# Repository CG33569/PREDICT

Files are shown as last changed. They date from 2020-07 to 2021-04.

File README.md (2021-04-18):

# PREDICT Project #

PREDICT Project at Aalborg University (AAU). This project is shared with Technical University of Denmark (DTU).
The project is focused on drone flight controller design and development, using a Real-Time Operative System implemented on a FPGA.

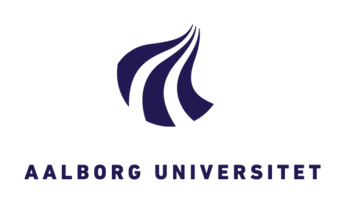
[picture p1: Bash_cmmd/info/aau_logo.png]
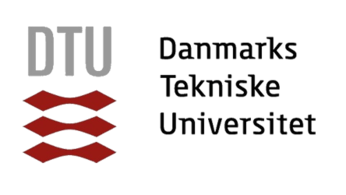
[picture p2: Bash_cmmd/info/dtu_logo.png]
 





### Repository structure ###

##### Documentation #####

An overview and general description of this project is included in Microsoft Power Point format, see the Predict Handover presentation.pptx file.

On top of that, the complete report is also included in PDF format, see the Predict_doc.pdf file. For more details, the original Latex files of the document are inside the Predict_doc folder. In case of needing to re-build the document, use doxigen or pdflatex commands, such as:

```
cd ~/REPO_LOCATION/PREDICT/Predict_doc && pdflatex main.tex
```

The documentation provides a detailed description about the project goals, functionalities and implementation. Additionally, it includes at the end two appendices as tutorial chapters to build a drone, calibrate it and run the flight controller on it.

##### Hardware - Drone desgin #####

Two models (A and B) were developed for this project. The related files are on the folder hardware_design, which contains:

* Printed Circuit Board (PCB folder): a custom board desgined for this project, which connects all the components to the controller. Designed with DipTrace

* Mechanics design (CAD_files folder): all the body and custom parts assembly for both models. Done in Solidworks 2019.

* Simulation model (simulation folder): both models A and B imported into CoppeliaSim simulator and additional dependencies for using the flight controller with the simulator.

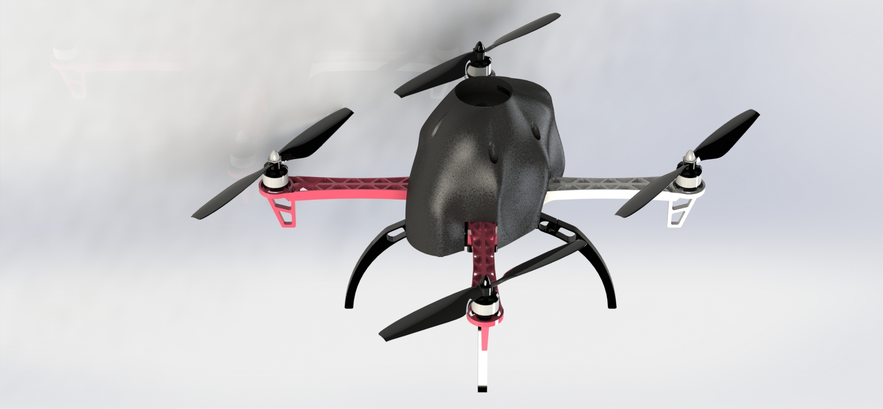
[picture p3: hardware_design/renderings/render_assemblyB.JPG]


##### Software - Flight controller and other applications #####

The flight controller is designed for the Patmos architechture, specifically for the de10-nano FPGA. A copy of this architecture is on the flight_controller/de10-nano-drone folder, which is a project on Quartus Prime.

The flight controller works as an application on that runs on top of the Patmos architecture. This C application is located on the flight/controller/de10-nano folder and it has the following:

* Basic functionalities (basic_lib folder): header and external files with global variables, low-level and functionalities related mostly to Patmos and communication.

* Components (sensors folder): header files for handling and using all the components.

* Flying functionalities (FC_functionalities folder): header files for calibration and flying modes available.

* Test programs (sensors_tests folder): header and script files for running the test programs.

* Main flight controller files (Flight_controller_v2.c and PREDICTthread.h).

##### Others #####

In case of being new to Patmos architecture, the folder Bash_cmmd contains scripts and configuration files that are useful to download, compile and build the T-Crest repositories and also for downloading C-apps in a de10-nano board. 
These scripts and files are explained in detail in the Predict documentation, on the Appendices (Chapters 7 and 8).

##### References #####

The main reference for this project is the Arduino Quadcopter project from [Brooking](http://www.brokking.net/ymfc-32_main.html) and part of his project is on the Arduino_project folder. 

Apart from that, all other references are listed on the Predict project documentation, the Bibliography section.

-----------------------------------------------

### Authors ####

* Carolina Gomez Salvatierra, cgomez19@student.aau.dk

* Rahul Ravichandran, rravic19@student.aau.dk

* Mark Adamik, madami15@student.aau.dk

Supervisor: Anders la Cour-Harbo, alc@es.aau.dk

-----------------------------------------------

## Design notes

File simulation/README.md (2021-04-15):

# PREDICT Drone in CoppeliaSim #

This a test-application for connecting the DE10-Nano FPGA to the CoppeliaSim simulator and try to use the flight controller on it. The idea is that the user can control the drone with the transmitter, the flight controller runs on the board but it gets the feedback and moves the drone in the simulation.

### Simulator CoppeliaSim set-up ###

Download the simulator (version EDU) from its [official website](https://www.coppeliarobotics.com/downloads).

Use the ExternalAPI to access from the FPGA-Simulator Interface the components inside the simulator.

Make sure you have following files in your directory, in order to run the various examples:

1. sim.py
2. simConst.py
3. the appropriate remote API library: "remoteApi.dll" (Windows), "remoteApi.dylib" (Mac) or "remoteApi.so" (Linux)
4. simpleTest.py (or any other example file) <- Run this script to verify that the connection between Coppelia and a Python scrip is successful.
5. Launch and start the simulation in drone_remoteAPI.ttt.

### FPGA and application set-up ###

1. Download on the FPGA the Quartus project "de10_nano_drone_simulator.jic" and re-start the board.
2. Connect the receiver and a UART-USB adapter on the uart3 of the board. See bellow the GPIO0 pins:

```
       * *
       * *
       * *
       * *
       * *
       * *
       * *
       * *
txd 26 * * 25 rxd UART3
AC3 24 * *
AC3 22 * *
AC3 20 * *
AC2 18 * *
AC1 16 * *
AC0 14 * *
       * *
       * *
       * *
       * *  
       * *  
txd  2 * *  1 rxd UART
```

Before doing the next steps, start the simulation in CoppeliaSim.

3. Download this C application as the simulation.c file as the main script.
4. At the same time, launch the main.py on the PC, which works as an interface between the simulator and the FPGA.

```
+--------------+         +--------------+         +-------------------+
|     FPGA     | <-----> |  Interface   | <-----> |     Simulator     |
| simulation.c |         |    main.py   |         |drone_remoteAPI.ttt|
+--------------+         +--------------+         +-------------------+
                        |___________________ PC ______________________|
```

##### Future works #####

* The current code only gets the receiver chanels 0-3 values on the simulation in order to spin the motors, but there is no controller avaliable yet.
* Improve the physics dynamics on the drone body so it can be controlled with a PID.
* Re-write the main multicore-flight-controller in order to get the sensor values from the simulation.

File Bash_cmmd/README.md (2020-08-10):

# Instructions #

These scripts and files are to meant to help to build patmos and download c code on the boards DE2-115 and DE10-nano. Some of the commands are in a script to automatically do it:
* To update repositories:
```
./fpga_update
```

* To build and download patmos with a "hello world" c code, specify the board on the MakeFile (see next section, step 3) and run one of these two:
```
./fpga_de2115
./fpga_de10
```

* After downloading the Patmos architechture on a board, there is a script for apps. To make things easier, the script is on the c_apps folder in this repository, which directly copies a c app developed on this repository to the Patmos directly and compiles+downloads it on the board:
```
cd .. && cd c_apps
./runthis
```

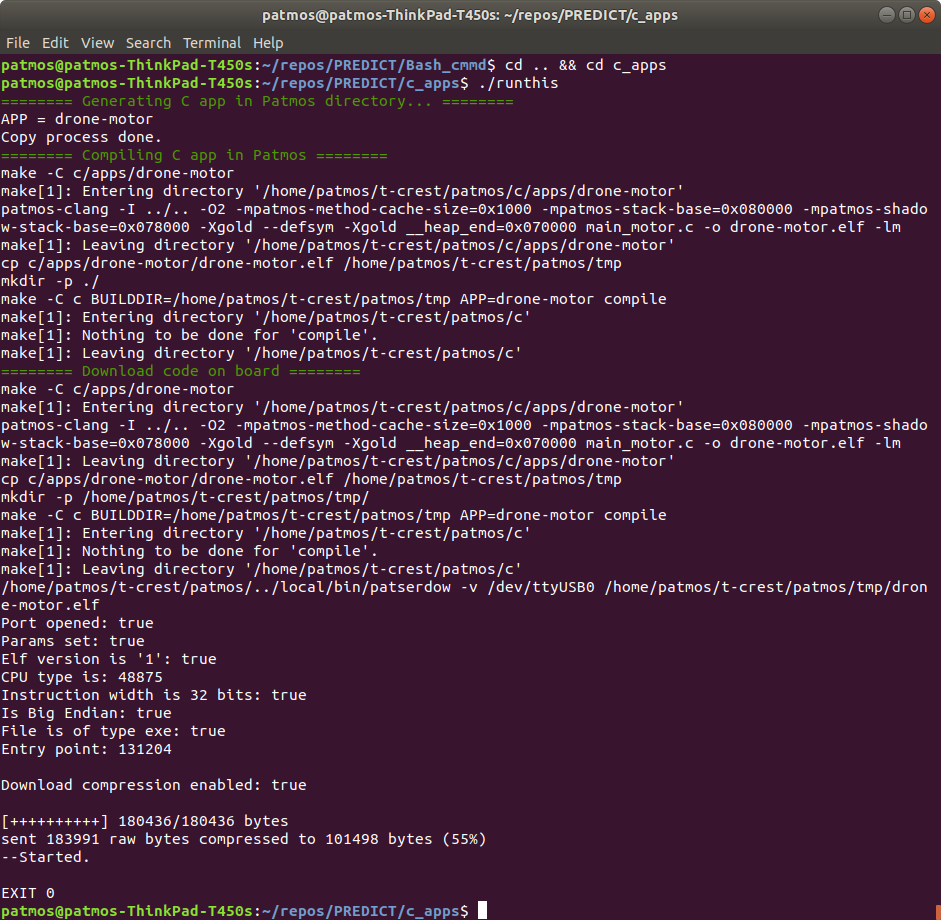
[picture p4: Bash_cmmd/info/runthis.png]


The next sections of this README file explains step by step how to update, build and download Patmos and c apps on the boards.

The file patmos_help.txt contains just a set of used instructions to go through. Some of them are listed here, and some of them are just information or ideas that could be used later.

### Building PATMOS ###

1. It's necessary to update the repositories, not just patmos, but also other libraries and dependencies among with it, you should have a folder called "t-crest" which contains at least three repositories: patmos, newlib and misc.
```
cd ~/t-crest
./misc/gitall pull
```

2. After pulling and updating all the repositories, build the libraries. Before running the following commands, delete the directory t-crest/newlib/build.
```
./misc/build.sh
```

In case of having some trouble building the libraries, you can try:
* Building only the newlib.
```
./misc/build.sh newlib
```

* Building everything from inside the misc folder and then re-try the newlib.
```
cd misc
cp build.cfg.dist build.cfg
./build.sh
cd ..
./misc/build.sh newlib
```

3. Modify the MakeFile inside the patmos repository, to specify the board and hardware connection type. Only necessary to (un)comment the BLASTER_TYPE and BOARD values.

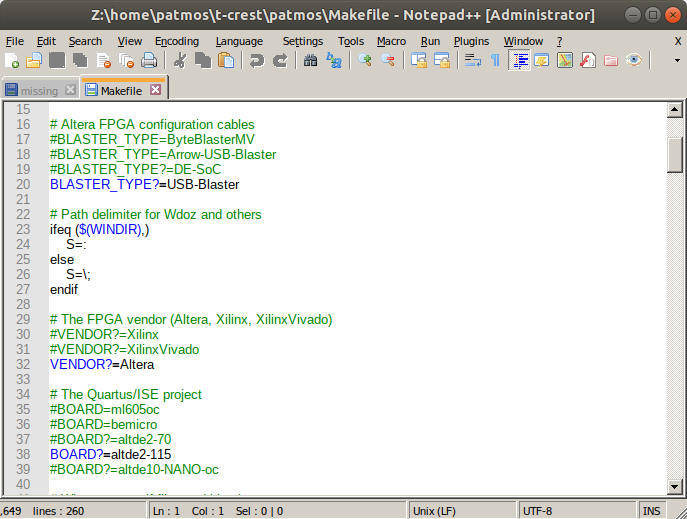
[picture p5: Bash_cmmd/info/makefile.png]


4. FPGA de10-nano only: the 2nd UART (GPS) has a 9600 Baud Rate. Since this has not been officially updated yet, the .xml file must be modified and the configuration re-built. There is a copy in this repository of the file which can be copied.
```
rm -rf ~/t-crest/patmos/hardware/build
rm -rf ~/t-crest/patmos/hardware/config/de10-nano.xml
cp ~/PREDICT/Bash_cmmd/de10-nano.xml ~/t-crest/patmos/hardware/config
```

5. Finally, build the patmos architechture for the board, which includes building its corresponding Quartus Prime project.
```
cd ~/t-crest/patmos
export BOARD=de10-nano
make gen
make -C hardware verilog BOOTAPP=bootable-bootloader BOARD=de10-nano
make synth
```

6. Optional: re-build the architecture tools.
```
cd ~/t-crest/patmos
make tools
make clean
```

### Downloading PATMOS ###

1. Make sure that the Quartus Project was built correcty, either on Quartus Prime or through the terminal (see previous section).

2. Check that the board-laptop communication is running properly. The best way is to kill the process and re-start it.
```
cd ~/t-crest/patmos/
sudo killall -9 jtagd
jtagconfig
```

In case of errors or that the detection is taking too long, repeat the commands. This screenshot shows the connection of the two boards (DE-SoC for de10-nano and USB-Blaster for DE2-115):

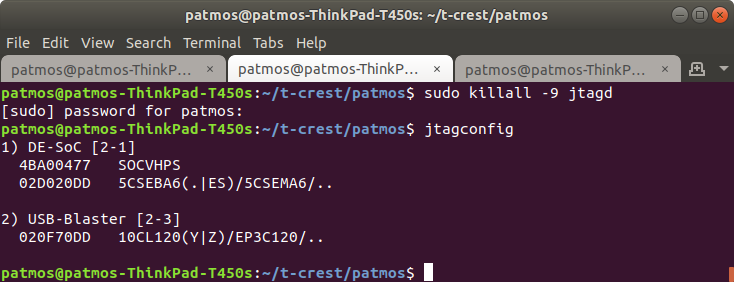
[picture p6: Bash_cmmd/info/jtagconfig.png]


3. This process is different for each board:

* For the DE2-115: run the following command on the terminal:
```
make config
```

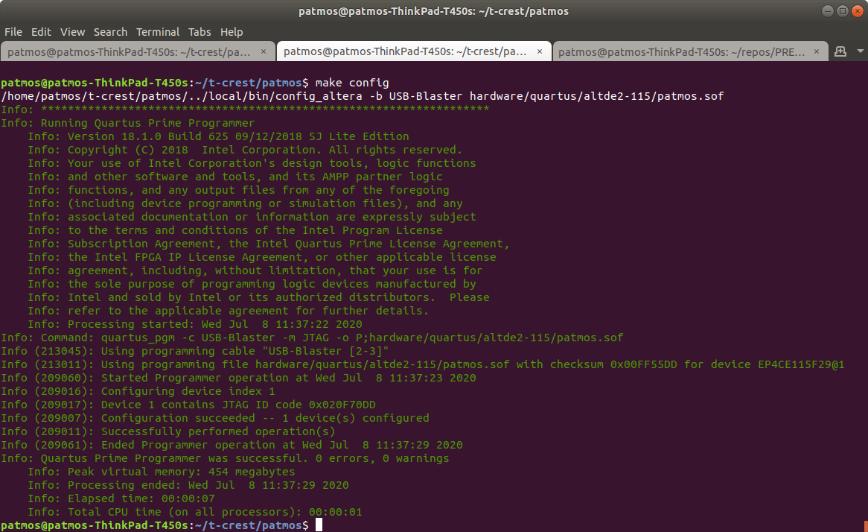
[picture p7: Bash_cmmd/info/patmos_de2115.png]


* For the DE10-nano: download the project through Quartus Prime:
	- Open Quartus Prime and the project ~/Location patmos directory here/patmos/hardware/quartus/de10-nano/patmos.qpf
	- Compile the Design (necessary to do this once). This project should be compiled without errors, if errors were given, check the update and building repositories process.



- Open "Program Device" (under "Compile Design" and "Edit Settings").
- Select the Hardware set-up and download the project.

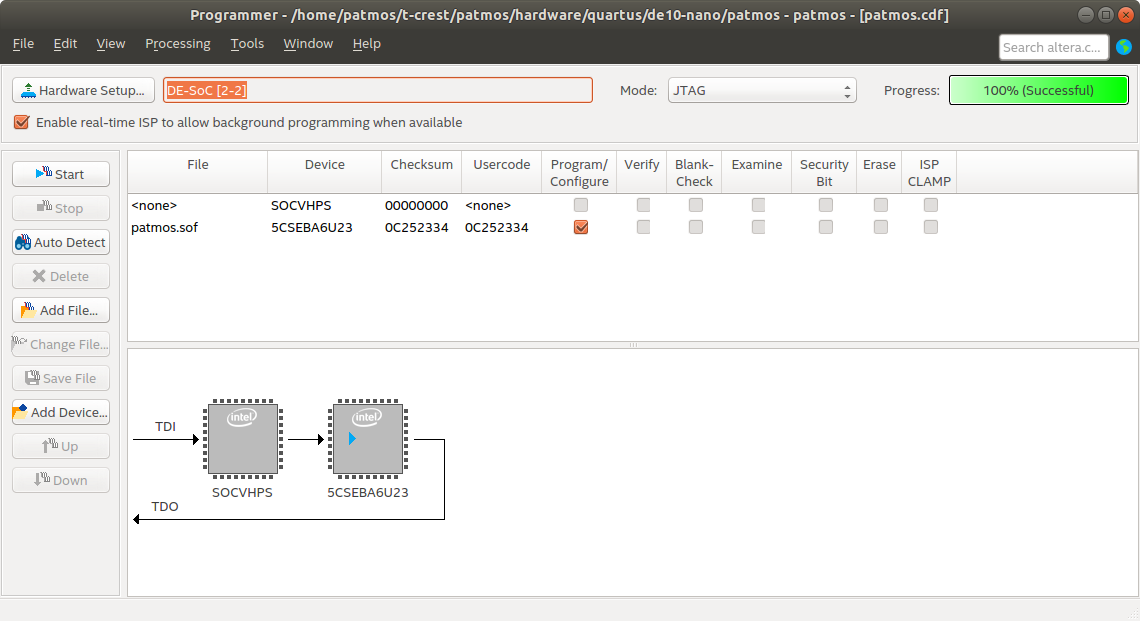
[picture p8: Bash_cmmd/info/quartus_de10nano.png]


If any errors were given associated to the JTAG, rerun the jtagconfig commands.

### Building c code for PATMOS ###

1. Create a folder for it on the directory ~/Your patmos location here/c/apps.

*A simple .c file*

2. Place in that folder your .c code and all its dependencies and .sh libraries.

3. Convert the .c code in an application. The ouput is an .elf file that must be located on the /tmp/ folder.
```
cd ~/Your patmos location here/patmos/c/apps/your folder here
patmos-clang -o ~/t-crest/patmos/tmp/hello.elf hello.c
```

Now the name of the app should be the same as the .elf file and it's the one that is going to be downloaded on the board.

*More complex apps*

2. Place in the folder the .c files, .sh .h libraries and a Makefile. Tip: include an additional .elf file generation on the tmp folder, to make sure that the code is updated before downloading.
```
	patmos-clang -I ../.. -O2 $(LDFLAGS) $(MAIN).c -o de10-IMU.elf -lm
	patmos-clang -I ../.. -O2 $(LDFLAGS) $(MAIN).c -o ~/t-crest/patmos/tmp/de10-IMU.elf -lm
```

3. Build the complete folder. Take the other apps as examples. This is possible through two ways:

* The Makefile specifies a concrete set of variables and has different options (e.g. compile, sim, clean,...). Usually is enough as long as it includes the conversion to an .elf file with the name of the app. In case of using an example app, check which command is the one that converts to .elf file after compiling.
```
cd ~/Your patmos location here/patmos/c/apps/your folder here
make
```
* Compile it through Patmos directly:
```
cd ~/Your patmos location here/patmos
make app APP=your app comp
```

The next screenshot shows the content and commands to build the example app tte-flight:
* Top-left: application files.
* Bottom-left: command terminal.
* Right: Makefile content.

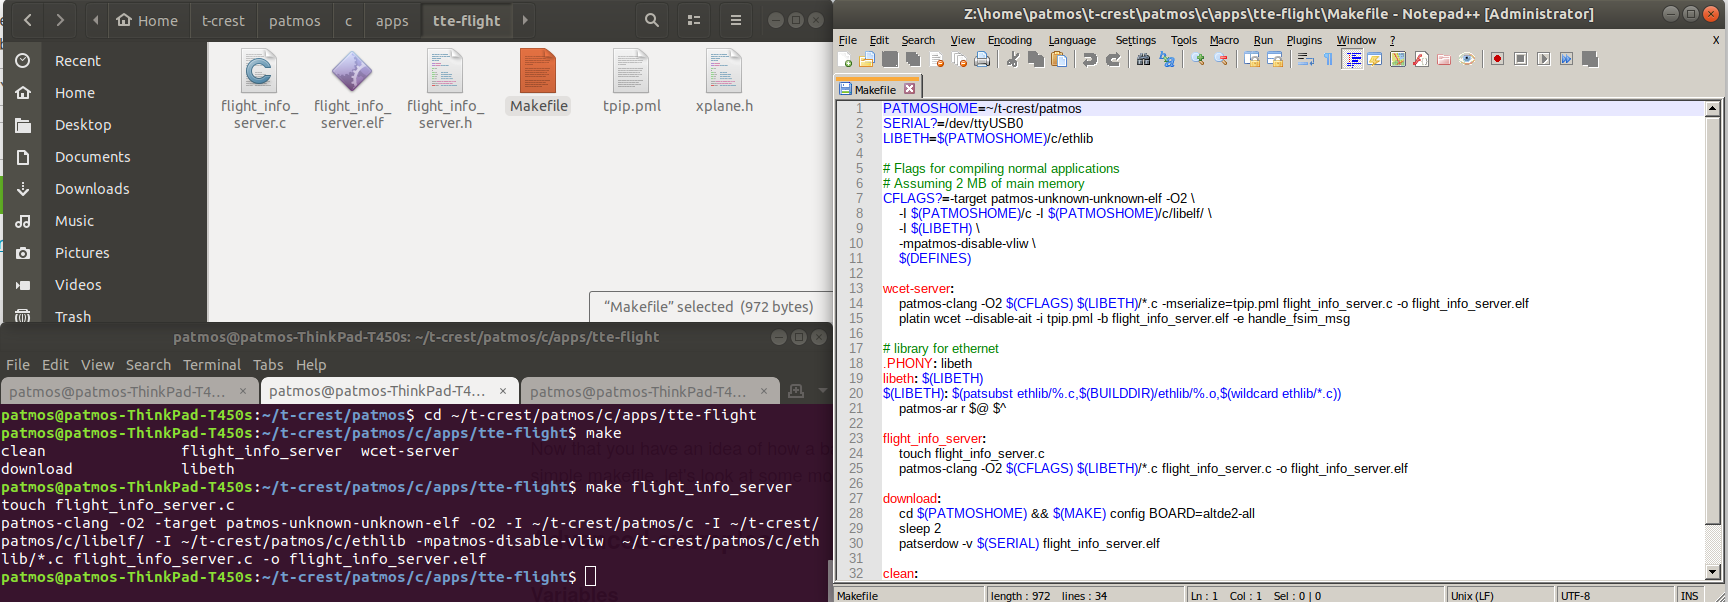
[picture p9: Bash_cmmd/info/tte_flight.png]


4. Further development:
* In this repository there are two c apps included: de10-nano and de10-IMU.
* de10-nano is an example app from the original patmos repository to test the communication with an IMU. To use it on the board (after downloading patmos on it):

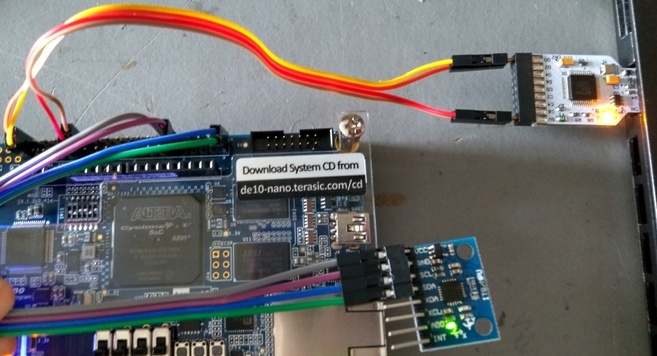
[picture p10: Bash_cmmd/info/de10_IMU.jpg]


```
cd ~/t-crest/patmos
make app APP=de10-nano download
```

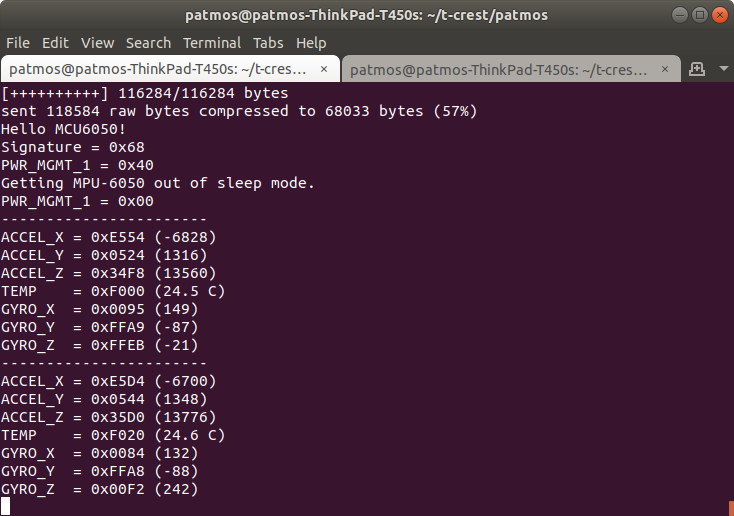
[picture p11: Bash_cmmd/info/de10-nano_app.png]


### Downloading c code ###

1. Specify FPGA drivers connection on your ubuntu computer. See the 51-usbblaster.rules file in this repository and copy it to your laptop, on /etc/udev/rules.d
In case this file is already on your computer, check its content is the same.

2. Reload the rules and add your log-in user to be allowed to access the connection ports. Then log-out and log-in again.

```
sudo udevadm control --reload
sudo usermod -a -G dialout $USER
```

3. The process done through the additional UART ports on the boards, so it's necessary an adapter UART-Usb.
* For the DE2-115: there is a complete UART port one the board and adapters have been provided by the Componenten lab.
On the picture: top cable -> USB cable to download patmos, bottom cable -> UART-USB cable to download c code apps.

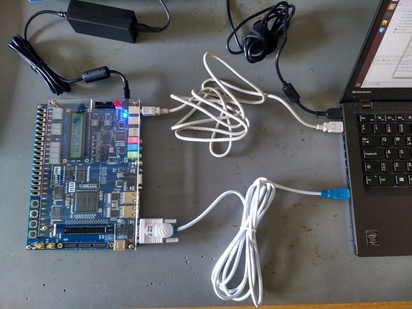
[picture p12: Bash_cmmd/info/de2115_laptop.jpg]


* For the DE10-nano: there is no port, so the Quartus Prime project has designed an UART connection through the I/O pins. So it is necessary a special adapter to connect the laptop to the board.
* WARNING!: download patmos on this board BEFORE connecting its UART to the laptop. Otherwise a shortcout could happen.
* Follow the instructions of the README.md file on the directiory /patmos/hardware/quartus/de10-nano to set up the switches and pins for the UART.
* Connect the UART pins to the adapter. Here there is an example:
```
Pin+Number | Wire colour | Adapter
------------------------------------
    rxd 1  |    white    | rxd
    txd 2  |    grey     | txd
   3.3V 29 |    purple   | VBUS
    GND 30 |    blue     | GND
```
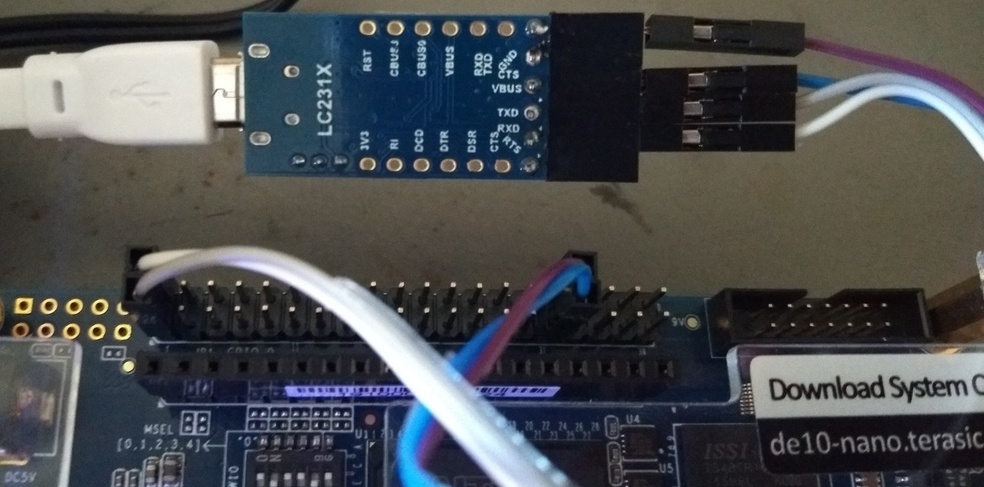
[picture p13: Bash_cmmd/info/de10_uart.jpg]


4. Connect the board(s) to the laptop. If the connection has been successful, the directory /dev/ a special file "ttyUSB0" should have been generated. If not, check steps 1 and 2 and plug the board again.

5. Download the built app (.elf file) on the board.

```
cd ~/Your patmos location here/patmos
make BOOTAPP=bootable-bootloader APP=hello_puts tools download
```

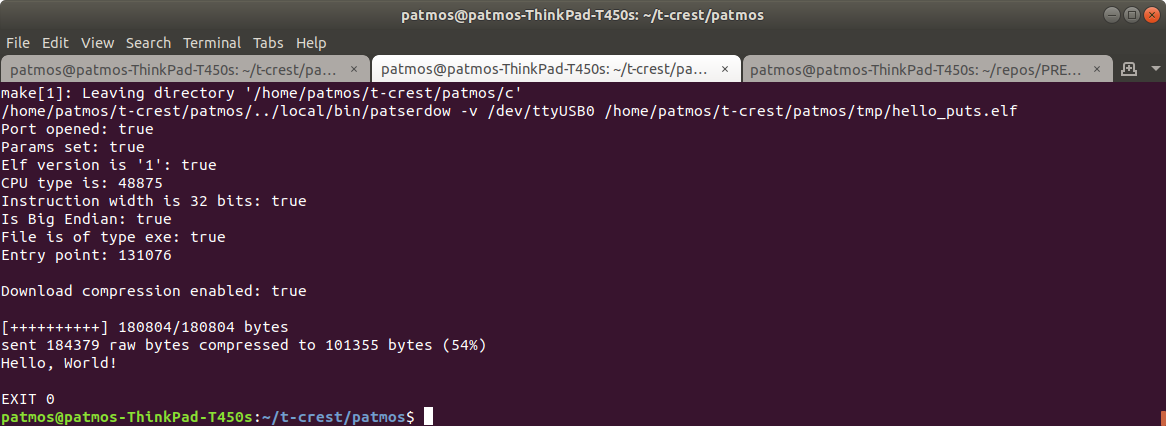
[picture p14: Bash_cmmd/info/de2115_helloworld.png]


In case of error:
* _Port not found_ : review the rules and UART-USB connection.
* _Port denied_ : review the user access.
* _Receiver did not reply correctly (expected 62 got 10)_ : this can happen with any other numbers for "expected" and "got". Once a c app has been successfully downloaded, the UART is usually no longer receptive to download apps. To fix this, re-plug the USB-UART to the laptop (maybe more than once). If after some tries, it still does not work, reload patmos and the app. Try to re-start the board as well.
* (After downloading process) _Exception Timeout_: problem with the bus wires. The laptop was able to communicate with the bus, but the info did not reach the board. Review the pins/cable adapter and re-boot the FPGA.
* Other errors: maybe it's a hardware problem change cable or re-try with another board if the two previous points are OK. For more info, review the pins assignment and the corresponding manuals.

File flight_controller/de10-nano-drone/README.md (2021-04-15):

# DE10 Nano Configuration for Patmos

Set the board variable `BOARD=de10-nano` (best done in a local config.mk)

Change switches for FPGA configuration to:

```
+------+
|* ** *|
| *  * |
+------+
```

Probably add USB blaster permissions for: Bus 001 Device 005: ID 09fb:6810 Altera and 09fb:6010

A TTL UART is connected to GPIO pins 1 and 2 of GPIO 0. The pins 38, 39, and 40 for the DTU I2C controller. Pins 6 and 5 are for the second UART and pins 24 - 13 are for the actuators and propdrives. Additionally, the UART3 and ADC Modules were added for the PREDICT Project. See below.

```
GPIO 0
____________________________
SCL 40 * * 39 SDA
AD0 38 * *
       * *
       * *
    34 * * 33 AD0
SDA 32 * * 31 SCL
GND 30 * * 29 3.3V
       * *
txd 26 * * 25 rxd UART3
AC3 24 * *
AC3 22 * *
AC3 20 * * 19 PROP3
AC2 18 * * 17 PROP2
AC1 16 * * 15 PROP1
AC0 14 * * 13 PROP0
GND 12 * * 11
       * *
       * *
txd  6 * *  5 rxd UART2
     4 * *  3
txd  2 * *  1 rxd UART
____________________________

ADC Module
____________________________
         9 * *  10 GND
         7 * *
         6 * *  5  GND
         4 * *  3
battery  2 * *  1  VCC5 
feedback
____________________________

```

rxd and txd are from the Patmos view, therefore TTL UART rxd needs to
be connected to txd and the other way around.

FPGA configuration has to be done via Quartus (instead of make config).

The on-chip memory is 512 KB (instead of typical 2 MB on the DE2-115).
Therefore, the stack start needs to be set accordingly with following
linker options:

```
        -mpatmos-stack-base=0x080000 -mpatmos-shadow-stack-base=0x078000 \
        -Xgold --defsym -Xgold __heap_end=0x070000
```

Best see in the example in c/apps/de10-nano. 

Alternatively, it is possible to use the external 1 GB DDR3 memory. In
de10-nano-drone.xml comment the line
```
<ExtMem size="500k" DevTypeRef="OCRam" />
```
and uncomment the line
```
<ExtMem size="1g" DevTypeRef="DDR3Bridge" />
```
Additionally, download the "DE10-Nano_v.1.3.8_HWrevC_SystemCD.zip" demo cd from 
```
http://download.terasic.com/downloads/cd-rom/de10-nano/
```
and write the SD card image from Demonstrations/FPGA/SdcardImage
to an SD card which is inserted into the SD card slot of the de10 Nano.
Power on the board, and after a few seconds, program the FPGA,
allowing the FPGA to access the DDR3 memory controller.

Compile and download that example with:

```
make app APP=de10-nano download
```

This example uses the DTU controller to print our the values of the accelerometer, thermometer, and gyroscope. You can use the program that reads out from the AAU
interface with:
```
make app APP=de10-nano MAIN=blinking download
```

The acts_props_uart2 application provides the functions to interact with the actuators, propdrive, and to the second UART. N.B. only the second UART was tested. I have no way to test the actuators and propdrive. Compile and download that example with:

```
make app APP=de10-nano MAIN=acts_props_uart2 download
```

## Comments

 * The I2C interface is an adaption of the [I2C Master](https://www.digikey.com/eewiki/pages/viewpage.action?pageId=10125324) from Digi-Key,
   where further information on the interfacing can be found
 * Register definitions in C for the MPU-6050 can be found at https://playground.arduino.cc/Main/MPU-6050

## TODO

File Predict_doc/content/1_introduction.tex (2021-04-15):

\chapter{Introduction}\label{ch:intro}

Patmos is a time-predictable Very Long Instruction word (VLIW) processor developed by Denmark Technical University(DTU). Patmos architecture is a part of the T-Crest Project \cite{bib:t-crest}, whose results were published in  \cite{SCHOEBERL2015449}.  This project describes the construction and development of a quad-copter and its flight controller integrated with the Patmos processor developed by the DTU.

The GitHub repository for the project containing all the test codes and the flight controller code can be found at \cite{bib:multicore_repo}.

\section{Previous works}
% the Arduino guy
This project has been built on top of other researchers and people's work. The most relevant reference is the project YMFC-32 from Joop Brooking\cite{bib:brooking}, the STM32 quad-copter is a DIY low-cost drone with common components that uses an Arduino board for the flight controller development. His work has been very relevant for the flight controller development and electronics design.

% Where we got our additional libraries from
For more specific functionalities, there are also multiple resources for practical Real-Time applications and embedded systems, such as filters, operations or libraries. 
This is the case of the Kalman filter developed by Lauszus\cite{bib:kalmanAAU} and the GPS library by  McGladdery \cite{bib:gpsLib}, whose work has also been used in this project for filtering sensors data and accessing the GPS data.

And in the scenario of using the Patmos architecture, there is Michael Platzer and Emad Jacob Maroun \cite{bib:tu_viena}, who presented a controller for the position of a drone using an IMU. Their work on the I2C communication and corresponding files have been used in this project. 

The fixed point library used in this project is an extension of the code developed by Tim Hartrick and Ivan Voras \cite{bib:fixedpth}.

\section{Problem analysis and project goals}\label{sec:prob_analysis}

The main focus of this project is to develop a drone concept with Patmos that is able to fly, either indoors or outdoors.

The flight controller should also use different features from Patmos and handle them, such as the multi-core for sharing and accessing data between the cores. 

The Patmos libraries has also a variety of functionalities for accessing a data through different communication protocols like Inter-Integrated Circuit (I2C), Serial Peripheral Interface (SPI), 
Universal asynchronous receiver-transmitter (UART) and also send/receive Pulse Width Modulation (PWM), and the board also counts with a set of General Purpose Input/Output (GPIO)  and an analog signals module. 

The Patmos architecture was provided in a Field Programmable Gate Array (FPGA), model De10-Nano and the libraries of Patmos were configured to work with the De10-Nano board. 

Overall, the goals of this project could be listed as follows:

\begin{enumerate}
    \item Design a complete drone, whose design uses different components required for an autonomous flight.
    \item Design a flight controller within Patmos architecture that integrates the different components through the different features provided by Patmos.
    \item The designed drone can take off, fly and land.
    \item The designed drone must be capable of hovering at a constant altitude and and also maintain its position.
    \item The design should be scalable, i.e. it can be easily replicated and reused.
\end{enumerate}

To reach these goals the next chapters in this document shall explain how the problem has been approach. Chapter \ref{ch:hw} presents the hardware design (mechanic and electronics) and Chapter \ref{ch:sw} describes the flight controller design and its features. Then the Chapters \ref{ch:impl} and \ref{ch:test} describes how the design has been implemented and how the libraries of the code provided is structured. Finally, the Chapter \ref{ch:concl} summarizes how the goals have been reached and comments on the project.

Apart from that, there are two additional chapters, Appendixes \ref{app:build} and \ref{app:setup}, which are rather tutorials and more technical explanation about how to mount and assemble the proposed design. These chapters have been written with the idea of being helpful for anybody that wants to replicate this project and/or build on top of it, so this type of reader has instructions and a guideline for doing so.

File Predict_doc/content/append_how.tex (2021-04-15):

\chapter{Appendix: how to set up the drone}\label{app:setup}
This appendix describes how to set up the drone to take off and it is useful for readers that are not that familiar with the Patmos architecture or that want to further develop the flight controller.
Most of the following sections show parts of scripts and commands that can be found on the Patmos Handbook \cite{bib:patmos_hnd} or in the support and complementary PREDICT repository \cite{bib:pred_repo}.

For the set up, it is necessary to use computer with Ubuntu 18 at least. In case of not having one, it is possible to use the Virtual Machine (VM) provided by the Patmos main webpage \cite{bib:patmos_page}.

On top of that, this project uses the multi-core feature, which needs the external memory on the microSD of the De10-Nano board. Before downloading Patmos on the board, it is necessary to flash the SD card in order to make it compatible with the system. Files available in \cite{bib:microSD} and detailed description on the README.md in the Quartus Prime project for de10-nano-drone.

\section*{Running Patmos on the board}
The model used in this project is the FPGA De10-Nano from Altera and the Patmos OS is implemented in a Quartus Prime project. To download it on the board from a computer, it is necessary to follow two processes: install Patmos dependencies on the computer and connect it to the board.

To install Patmos:
\begin{enumerate}
	\item Create a folder called "t-crest" on your home address.
	\item Download and rename the following repositories from the T-Crest project \cite{bib:tcrest_repo}.

\lstset{style=Bstyle}
\begin{lstlisting}[language=bash]
mkdir t-crest && cd ~/t-crest
git clone https://github.com/t-crest/aegean.git
git clone https://github.com/t-crest/argo.git 
git clone https://github.com/t-crest/patmos-compiler-rt.git compiler-rt
git clone https://github.com/t-crest/patmos-gold.git gold
git clone https://github.com/t-crest/patmos-llvm.git llvm
git clone https://github.com/t-crest/patmos-misc.git misc
git clone https://github.com/t-crest/patmos-newlib.git newlib
\end{lstlisting}

	\item Delete the previous build folders.

\begin{lstlisting}[language=bash]
rm -rf ~t-crest/newlib/build
rm -rf ~t-crest/patmos/hardware/build
\end{lstlisting}

	\item Re-build and compile the libraries

\begin{lstlisting}[language=bash]
cd misc
cp build.cfg.dist build.cfg
./build.sh
cd ..
./misc/build.sh newlib
cd patmos/doc
make
\end{lstlisting}
	
	\item Check if the commands are available.
\begin{lstlisting}[language=bash]
Still on process
\end{lstlisting}

    \item In case that Patmos has been updated (new features has been added, another model has been included, etc), it is necessary to update accordingly.
    
\begin{lstlisting}[language=bash]
cd ~/t-crest/
gitall pull
# Repite build and compilation process from here
\end{lstlisting}    

\end{enumerate}

To download Patmos on a de10-nano board for the first time, it is necessary to set up some additional configuration:
\begin{enumerate}
	\item Install the FPGA drivers on the computer. The drivers must be located on the /dev/ folder, in a file. It's possible either to copy the file \textit{51-usbblaster.rules} from the complementary repository\cite{bib:pred_repo} or generate it with the following content:
	
\lstset{style=OtherSt}
\lstinputlisting{Figures/setup/Files/51-usbblaster.rules} 	

	\item Give to the computer user account the right to access the communication ports.
	
\lstset{style=Bstyle}
\begin{lstlisting}[language=bash]
sudo usermod -a -G dialout user
# Now log out from the computer and sign in again
\end{lstlisting} 

	\item Connect a FPGA to the computer and check if it can be recognised.
	
\begin{lstlisting}[language=bash]
jtagconfig
# In case the command gets stuck, kill it and re-run it
sudo killall -9 jtagd
\end{lstlisting} 	

%\end{enumerate}

\begin{figure}[H]
    \centering
        
    \caption{Running the jtagconfig command shows every connected FPGA. In this case, it shows a de10-nano (De-SoC) on port 2-1 and a de2-115 (USB-Blaster) on port 2-3.}
    \label{fig:jtagconfig}
\end{figure}

Finally, to download the Quartus Prime project on the board it is necessary to compile the Patmos folders according to a certain model. Afterwards, the FPGA shall retain the architecture in its memory even after turning on and off. 
In case a C app does not run correctly, repeat only the last steps inside Quartus Prime. In case the issue still persists, repeat this procedure:
%\begin{itemize}
    \item Check that selected board is de10-nano-drone and that the communication type is DE-SoC. This is set up in the Makefile located in \textit{~/t-crest/patmos}:

\lstset{style=Bstyle}
\begin{lstlisting}[language=bash]
# Altera FPGA configuration cables
#BLASTER_TYPE=ByteBlasterMV
#BLASTER_TYPE=Arrow-USB-Blaster
BLASTER_TYPE?=DE-SoC 
#BLASTER_TYPE?=USB-Blaster

# The Quartus/ISE project
#BOARD=ml605oc
#BOARD=bemicro
#BOARD?=altde2-70
#BOARD?=altde2-115
BOARD?=altde10-NANO-oc
\end{lstlisting} 
    
    \item Check the hardware configuration for the de10-nano-drone. For this flight controller, four cores are required and the sensors are distributed and assigned between the different cores. The configuration can be checked on the \textit{~/t-crest/patmos/hardware/config/de10-nano-drone.xml}:
    
\lstset{style=Bstyle}
\begin{lstlisting}[language=bash]
<patmos default="default.xml">
  <description>Configuration for de10-nano board for drone with external ddr3 memory</description>

  <frequency Hz="50000000"/>
  <pipeline dual="false" />
  <cores count="4" />
  <ExtMem size="1g" DevTypeRef="DDR3Bridge" />

  <IOs>
  <IO DevTypeRef="Uart1" offset="6" core="3"/>
  <IO DevTypeRef="Uart2" offset="7" core="3"/>
  <IO DevTypeRef="Leds" offset="9" core="0"/>
  <IO DevTypeRef="I2CMaster" offset="11" core="1"/>
  <IO DevTypeRef="Actuators" offset="12" core="2"/>
  <IO DevTypeRef="SPIMaster" offset="14" core="0"/>
  </IOs>

  <Devs>
    <Dev DevType="Uart1" entity="Uart" iface="OcpCore">
      <params>
        <param name="baudRate" value="9600"/>
        <param name="fifoDepth" value="16"/>
      </params>
    </Dev>
    <Dev DevType="Uart2" entity="Uart" iface="OcpCore">
      <params>
        <param name="baudRate" value="115200"/>
        <param name="fifoDepth" value="128"/>
      </params>
    </Dev>
    <Dev DevType="Leds" entity="Leds" iface="OcpCore">
      <params>
        <param name="ledCount" value="8"/>
      </params>
    </Dev>
    <Dev DevType="I2CMaster" entity="I2CMaster" iface="OcpCore">
      <params>
        <param name="i2cBitRate" value="100000" />
      </params>
    </Dev>
    <Dev DevType="Actuators" entity="Actuators" iface="OcpCore">
      <params>
          <param name="extAddrWidth" value="16" />
          <param name="dataWidth" value="32" />
      </params>
    </Dev>

    <Dev DevType="SPIMaster" entity="SPIMaster" iface="OcpCore">
      <params>
          <param name="slaveCount" value="1" />
          <param name="sclk_scale" value="1" /> 
          <param name="fifoDepth" value="6"/>
          <param name="wordLength" value="12"/>
      </params>
    </Dev>

    <Dev DevType="DDR3Bridge" entity="DDR3Bridge" iface="OcpBurst" />
    <Dev DevType="OCRam" entity="OCRamCtrl" iface="OcpBurst">
      <params>
         <param name="sramAddrWidth" value="19" />
      </params>
    </Dev>
  </Devs>
</patmos>
\end{lstlisting}
    
    \item Compile Patmos for the de10-nano-drone set up. This can be done either all at once or per steps. In case of errors, it is recommended to do it per steps according to the Handbook\cite{bib:patmos_hnd} and check where the compilation fails.

\lstset{style=Bstyle}
\begin{lstlisting}[language=bash]
cd ~/t-crest/patmos
export BOARD=de10-nano-drone
rm -rf ~/t-crest/patmos/hardware/build
make gen
make -C hardware verilog BOOTAPP=bootable-bootloader BOARD=de10-nano-drone
make synth
\end{lstlisting} 
    
    \item Open Quartus Prime. The de10-nano-drone project is located in \textit{~/t-crest/patmos/} \textit{hardware} \textit{/quartus/de10-nano-drone/patmos.qpf}. In the case the project is not compiled yet, run "Compile Design" on the Task bar, to convert the project to a .sof binary file. 

\begin{figure}[H]
    \centering
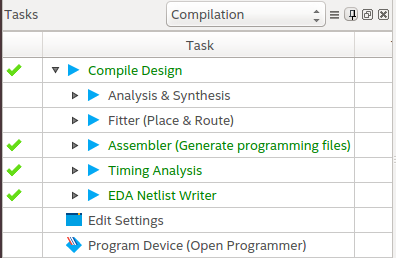
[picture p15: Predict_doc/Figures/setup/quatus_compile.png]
        
    \caption{If during the compilation in Quartus Prime errors were given, review the hardware settings, such as the board model, cores number, etc.}
\end{figure}

    \item By default, the compiled projects have the extension .sof and they are volatile, which means that after the FPGA is restarted, the Quartus project must be downloaded again. This is also an issue for using the multicore feature. To make the project permanent, it is necessary to convert the .sof into a .jic file. On Quartus Prime, go to \textit{Files/Convert Programming Files...} and generate the .jic file with the following options:
    
\begin{figure}[H]
    \centering
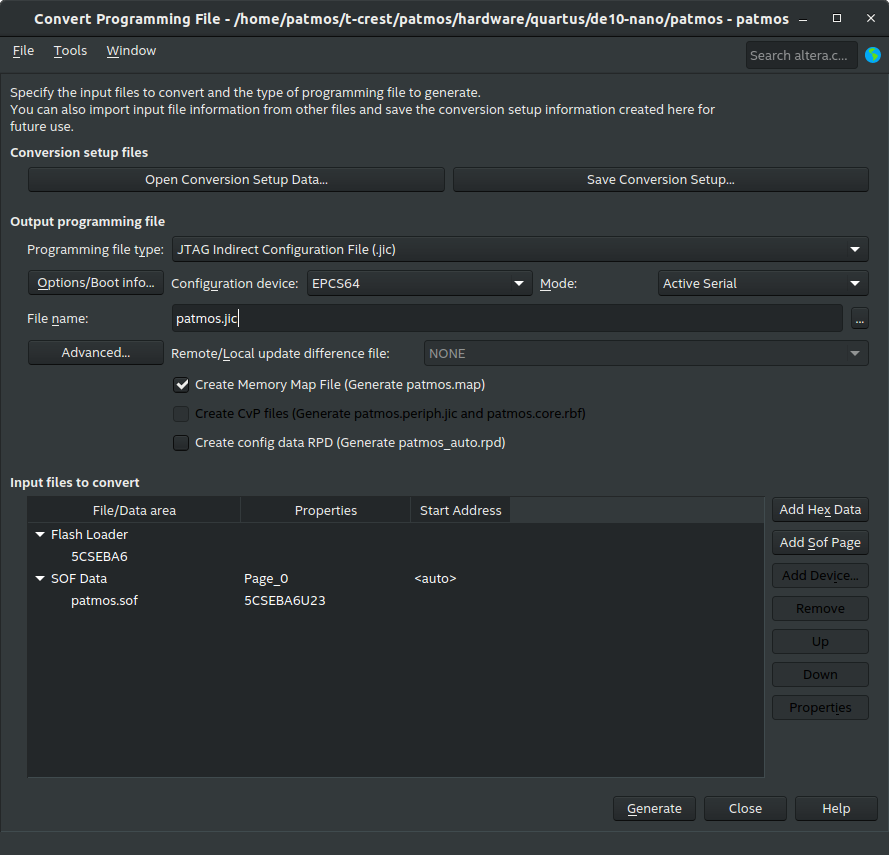
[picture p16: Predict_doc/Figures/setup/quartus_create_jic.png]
        
    \caption{Convert Programming Files options overview.}\label{fig:app_jic}
\end{figure}    
    
    \item Open the "Program Device" (see the Figure of the Task bar) and it will open a window for downloading the project on the board. Use "Hardware Setup..." to select the DE-SoC port and "Change Files..." to select the .jic project. Notice that it is also necessary to check "Factory default enhanced SFL image".

\begin{figure}[H]
    \centering
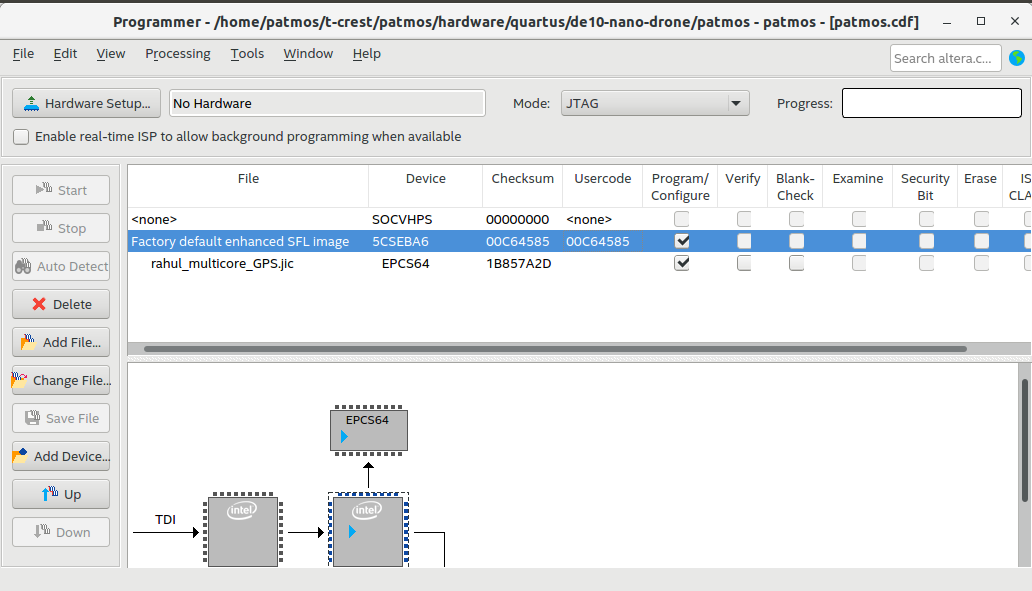
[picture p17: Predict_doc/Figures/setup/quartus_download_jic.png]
        
    \caption{Download de10-nano-drone project window.}
\end{figure}  
    
    \item After the project is downloaded, re-start the FPGA to be able to download C-apps.

%\end{itemize}
\end{enumerate}

\section*{C apps development through a "Hello World!" tutorial}

This tutorial explains how to create a "Hello World!" C application from scratch and run it on a board.
Before starting, it is necessary to have built and downloaded Patmos as mentioned in the previous sections.  

\begin{enumerate}
    \item Create a folder for the application inside Patmos' app directory. The directory must have the same name as the app.
\lstset{style=Bstyle}
\begin{lstlisting}[language=bash]
cd ~/t-crest/patmos/c/apps && mkdir hello   
\end{lstlisting} 
    \item Create a hello.c file inside the folder with the following content:
\lstset{style=Cstyle}
\begin{lstlisting}
#include <stdio.h>
#include <machine/patmos.h>
#include <machine/spm.h>

int main() {
  printf("Hello wrold!\n");
  return 0;
}      
\end{lstlisting} 
    \item Create a Make file inside the folder, which shall compile the .c file. The \textit{patmos-clang} command transforms the .c main file (and its dependencies) into a binary file compatible with the FPGA. This Makefile contains the following:
\lstset{style=OtherSt}
\lstinputlisting{Figures/setup/Files/Makefile}    
    \item Copy the generated file to the temp directory. This can be done as well inside the Makefile (uncomment last line).
    \item Go back to the main Patmos directory and download the app.
\lstset{style=Bstyle}
\begin{lstlisting}[language=bash]
cd ~/t-crest/patmos/
make APP=hello download
\end{lstlisting} 

\end{enumerate}

\begin{figure}[H]
    \centering
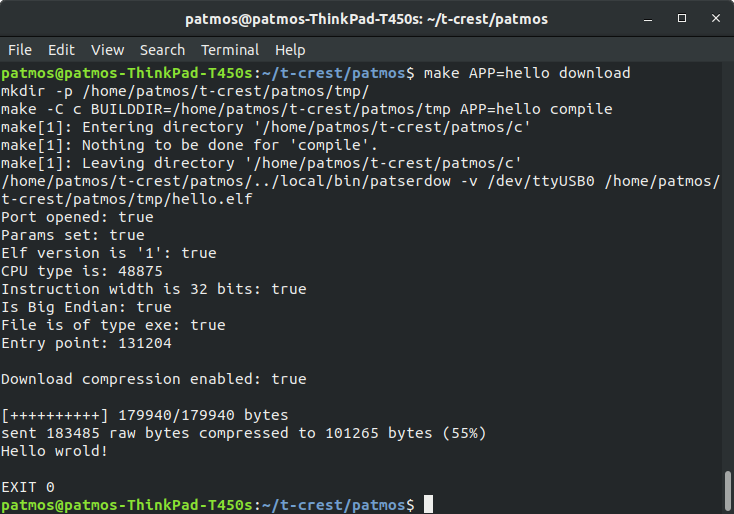
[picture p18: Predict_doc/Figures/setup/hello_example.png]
        
    \caption{Log and result on the terminal after downloading a C app.}
    \label{fig:c_app}
\end{figure}

\section*{Using the Flight Controller}\label{app:sec_fc}

The C-Application for the flight controller and its dependencies are in the \textit{~/t-crest/patmos/} \textit{c/apps/de10-nano/} directory. It contains the main script \textit{Flight\_controller\_2.c} in and the functions for each core are in the header \textit{PREDICTthread.h}. Apart from that, it also contains the following directories:

\begin{itemize}
    \item basic\_lib: contains low-level functions to access the pins and other Patmos-related options (such as counting time, etc). It also contains global variables to access the components and save their outputs, and the additional dependencies for using the GPS and barometer.
    \item FC\_functionalities: contains specific features for flying, such as the PID controller, take off, landing and calibration process.
    \item sensors: contains the handlers and implements the full functionalities for each sensor. These headers use the low-level functions from the basic library to access the sensors data and process it.
    \item sensors\_test: contains a set of different scripts. Each script is meant to be used of a specific single sensor or type of devices.
\end{itemize}
\subsubsection*{Pairing Transmitter and Receiver}\label{trans_receiver_pair}
To pair a transmitter and a receiver:
\begin{enumerate}
    \item Add the binding plug shorting the ground and the signal pins on the receiver.
    \item Power on the receiver and the receiver binding mode is indicated by fast blinking.
    \item Push the bind button on the transmitter and switch it on.
    \item The receiver is bound successfully if it stops blinking.
    \item Now remove the binding plug and the receiver is now paired.
\end{enumerate}

\subsubsection*{Change baud rate of Telemetry}\label{telemetry_baud}
The telemetry modules have to configured to be in the baud rate 115200 using a the software used by the telemetry module \cite{bib:ardupilot} (differs based on the provider of the module). 

\subsubsection*{Tuning the PID gains}
In case the behaviour of the flight controller needs to be tuned, the variables storing the PID gains can be found in the \textit{FC\_global.h} file in the \textit{basic\_lib} folder.

The recommended tuning procedure is described in Section \ref{app:tuning}.

\subsubsection*{Downloading the code}

To download this application on a board:

\begin{itemize}
    \item Select on the Makefile the main script (either the flight controller or one of the test programs available). All the dependencies have been included in this Makefile, do not change something else unless it is necessary.
    
    \lstset{style=Bstyle}
    \begin{lstlisting}[language=bash]
# Uncomment this for using the flight controller
MAIN?=Flight_controller_v2

# Uncomment and/or modify this for running a test program
# MAIN?=sensors_tests/receiver_test

# Modify this if another port is in used
SERIAL?=/dev/ttyUSB0

# Do not modify any further
I2C?=basic_lib/i2c_master
GPS?=basic_lib/gps
LDFLAGS?= \
        -mpatmos-method-cache-size=0x1000 \
        -mpatmos-stack-base=0x080000 -mpatmos-shadow-stack-base=0x078000 \
        -Xgold --defsym -Xgold __heap_end=0x070000

all:
	patmos-clang -I ../.. -O2 $(LDFLAGS) $(I2C).c $(GPS).c $(MAIN).c -o de10-nano.elf -lm
	patmos-clang -I ../.. -O2 $(LDFLAGS) $(I2C).c $(GPS).c $(MAIN).c -o ~/t-crest/patmos/tmp/de10-nano.elf -lm
download:
	patserdow -v $(SERIAL) de10-nano.elf
    \end{lstlisting} 

    \item Compile the App and download it.
    
\lstset{style=Bstyle}
\begin{lstlisting}[language=bash]
cd ~/t-crest/patmos/c/apps/de10-nano
make
cd ../../..
make APP=de10-nano download
\end{lstlisting} 

\end{itemize} 

\section*{Common troubleshooting}

\begin{itemize}
    \item Sensors and actuators: the different components can be tested individually with their own test programs. In case a specific device seems not to work properly, there are some approaches that you can try:
    \begin{itemize}
        \item In case of using the PCB for attaching the device, review the pins connection with a voltimeter. Follow the hardware diagram and connections shown in Chapter \ref{ch:hw}.
        
        \item In case of not using the PCB and connecting the device directly to the board, review the wiring and power supply. Sometimes it can be that two connections are accidentally switched (TX and RX, or SCL and SDA).
        
        \item Check that the device is not faulty and properly on. In a nutshell: IMU must light green, the barometer GPS+compass light red, the telemetry lights permanently green and the receiver red.
        
        In case the telemetry module is blinking green, it means it cannot reach its paired module, so it is necessary to review the connection between modules.If it permanently red is on configuration status, which means it needs to be connected to a computer with SikRadio \cite{bib:ardupilot} and its firmware needs to be re-uploaded. 
        
        In case the receiver is blinking-slow red, it means it cannot reach its paired transmitter, so review that the transmitter is properly on and paired to it. In case the receiver is blinking-fast red, it is on pairing mode and it needs to be paired with a transmitter and restarted afterwards, see Section \ref{app:sec_fc}.
        
        \item In case the device seems to be working fine, it could be that it is assigned to the wrong core or with the wrong settings. Review the hardware settings on the \textit{de10-nano-drone.xml}.
        
        Then modify Patmos configuration to single-core and with all the devices assigned to core 0. Then change the test program to one single thread with the function for that specific device.
    \end{itemize}
    
    \item Compiling Patmos: a server compiles and builds Patmos periodically to verify it is properly set, so it should not be a problem to build it and compile in a laptop.
    
    In case of compiling Patmos when it has been updated after some time, update not just the patmos repository, but all the repositories from the t-crest folder. Then follow the presented instructions for downloading Patmos on the board. Most of the building issues come from Step 4, where the libraries are built, so try to run the $./build.sh$ from another directory or rebuilding the newlib by steps.
    
    Also review that the board model is correctly specified as $de10-nano-drone$.
    
    \item Downloading Patmos: for this specific the project, the Patmos architecture is multicore, so review first the microSD card is correctly flashed and inserted. For this project the microSD cards were flashed in a Windows computer using Windiskimager32.
    
    Review afterwards the settings for the .jic file in Figure \ref{fig:app_jic} and remember to re-start the FPGA.
    
    \item Compiling C apps: use the Patmos dependencies libraries as presented in this project and other Patmos-app examples. 
    
    Also before downloading an app, review that the generated .elf files from the C code are updated. There is a difference between compiling an App from its own folder (it generates an .elf file there) than from Patmos main directory (it generates an .elf file on the $~/t-crest/patmos/tmp$ directory), so it can be that an App is built differently depending on the process and it can also be that the .elf file downloaded on the board is outdated. 
    
    For this project, the flight controller application was built on its own folder and the Makefile would create the two .elf files.

    \item Downloading C apps: here are some of the most common issues:
\lstset{style=Bstyle}
\begin{lstlisting}[language=bash]
java.util.concurrent.TimeoutException: Receiver did not reply (715 responses missing)
jssc.SerialPortException: Port name - /dev/ttyUSB0; Method name - openPort(); Exception type - Permission denied.
\end{lstlisting} 

Review that the user account has root privileges on the ports communication, on the steps 1 and 2 from downloading Patmos.
    
\lstset{style=Bstyle}
\begin{lstlisting}[language=bash]
java.util.concurrent.TimeoutException: Receiver did not reply (715 responses missing)
jssc.SerialPortException: Port name - /dev/ttyUSB0; Method name - closePort(); Exception type - Port not opened.
\end{lstlisting} 

Review that the FPGA drivers are properly installed and that not other process has not already access the port. Sometimes the easiest way is to disconnect the FPGA, re-start it and connect it again.

\lstset{style=Bstyle}
\begin{lstlisting}[language=bash]
java.util.concurrent.TimeoutException: Receiver did not reply (715 responses missing)
jssc.SerialPortException: Port name - /dev/ttyUSB0; Method name - openPort(); Exception type - Port not found.
\end{lstlisting} 

Review that UART-USB port is properly powered up (the drone should have the battery connected) and the port number matches what it is specified on the Makefile from $~/t-crest/patmos$.
    
\end{itemize}
% ===================================================================================
% Add this chapter to the table of contents:
%\addcontentsline{toc}{chapter}{Appendix: how to set up the drone}

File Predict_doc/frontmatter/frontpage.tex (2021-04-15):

\backgroundsetup{
scale=1.1,
angle=0,
opacity=1.0,  %% adjust
contents={}
}
% The geometry for this page is different and it is only applied in this section:
\begin{titlepage}

\newgeometry{top=0cm,bottom=1.2cm,right=0cm,left=0cm}
\BgThispage

%Top image
% For the ubuntu logo:
%  \centerline{\includegraphics[totalheight=0.568\paperwidth,width=1\paperwidth]{Figures/frontpage/frontpageimage1.jpg}}%
  \begin{center} 
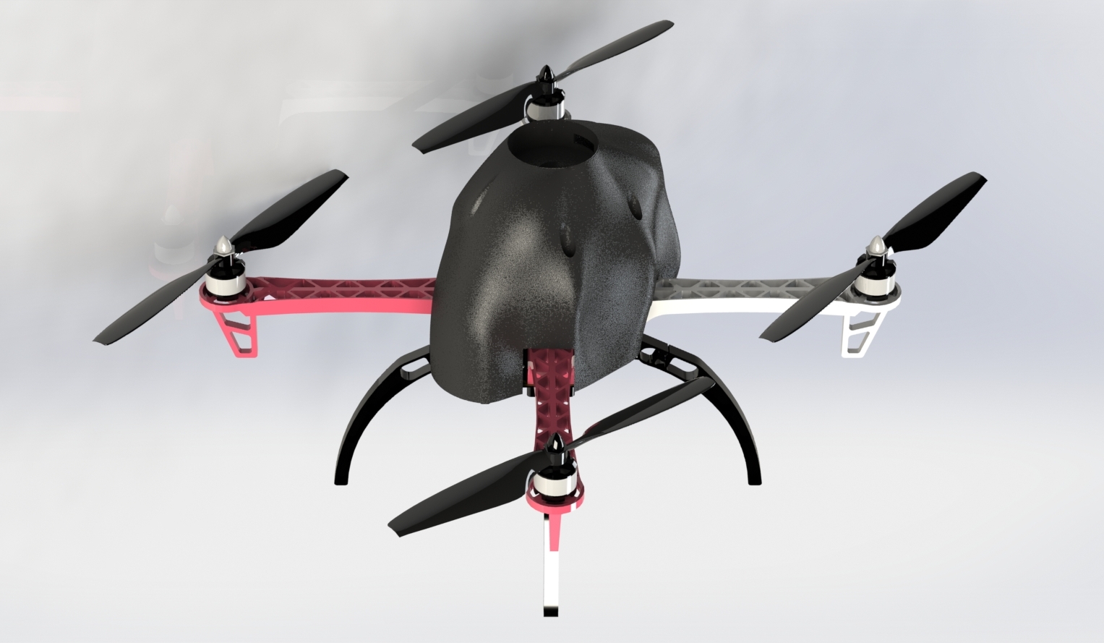
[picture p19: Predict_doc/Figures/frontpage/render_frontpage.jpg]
  \centerline{}% 
  \end{center}

%Title stuff	
	\vspace*{-0.96cm}
  {\noindent\color{aaublue}\fboxsep0pt\colorbox{white}{\begin{tabular}{@{}p{\paperwidth}@{}}
    \centerline{
    \begin{minipage}{0.85\textwidth}
        \bigskip
				\bigskip
        \centering
        \Huge{\textbf{PREDICT Project documentation}}
    \end{minipage}}
		
	\centerline{
	\begin{minipage}{0.9\textwidth}
        \bigskip
        \centering
        \Large{Working of a flight controller in a multi-core PATMOS architecture}
    \end{minipage}}
			
	\centerline{
	\begin{minipage}{0.9\textwidth}
        \bigskip
        \centering
        {\Large Carolina Gomez Salvatierra, Mark Adamik, Rahul Ravichandran}
    \end{minipage}}
			
    \centerline{
    \begin{minipage}{0.9\textwidth}
        \bigskip
        \centering
        {\large Department of Electronic Systems} 
    \end{minipage}}
			
    \centerline{
    \begin{minipage}{0.9\textwidth}
        \bigskip
        \centering
        {\Large 15th April, 2021}
        \smallskip
    \end{minipage}}
			
  \end{tabular}}}
  \vfill
  \begin{figure}[!b]
	\centering
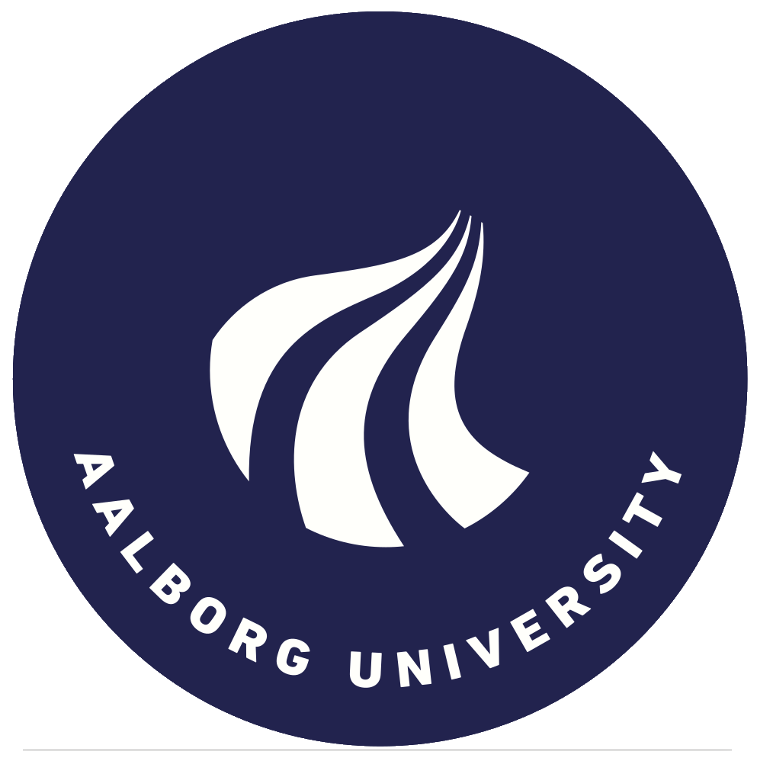
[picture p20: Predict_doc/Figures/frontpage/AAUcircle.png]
    
  \end{figure}

\end{titlepage}
\clearpage

\restoregeometry %Remember to set geometry defaults back after the page

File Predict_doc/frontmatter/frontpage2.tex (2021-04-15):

\backgroundsetup{
scale=1.1,
angle=0,
opacity=1.0,  %% adjust
contents={}
}
% The geometry for this page is different and it is only applied in this section:
\newgeometry{top=0cm,bottom=1.2cm,right=0cm,left=0cm}
\BgThispage
\begin{titlepage}
\vspace*{\fill}
  \noindent%
  {\color{white}\fboxsep0pt\colorbox{aaublue}{\begin{tabular}{@{}p{\textwidth}@{}}
    \begin{center}
    \Huge{\textbf{PREDICT Project documentation
    }}
    \end{center}
    \begin{center}
      \Large{How to deal with Patmos in a drone flight controller and not to die in the process}
    \end{center}
    \vspace{0.2cm}
   \begin{center}
    {\Large
      Carolina Gomez Salvatierra, Mark Adamik, Rahul Ravichandran}\\
    \vspace{0.2cm}
    {\large Department of IT and Electronics}
   \end{center}
   \vspace{0.2cm}

   \begin{center}
    {\Large \today}
   \end{center}
  \end{tabular}}}
  \vfill
  \begin{center}
     
  \end{center}
\end{titlepage}
\clearpage

\restoregeometry %Remember to set geometry defaults back after the page

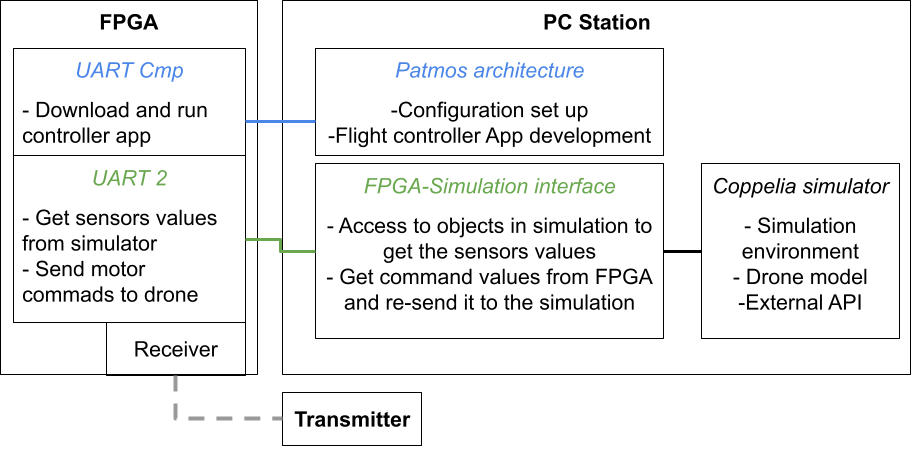
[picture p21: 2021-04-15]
Predict_doc/Figures/simulation/simulation_concept.png

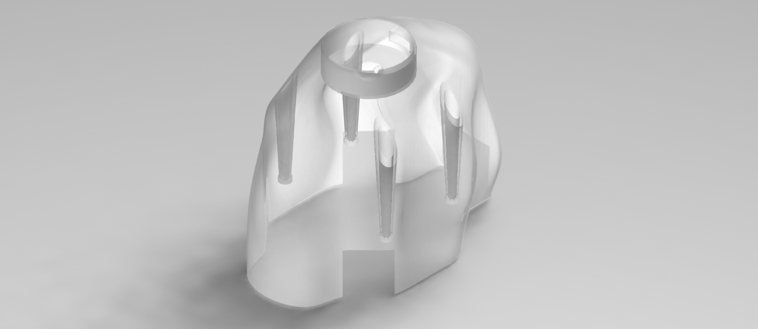
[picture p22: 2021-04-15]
Predict_doc/Figures/hardware/cover_transPlastic.JPG

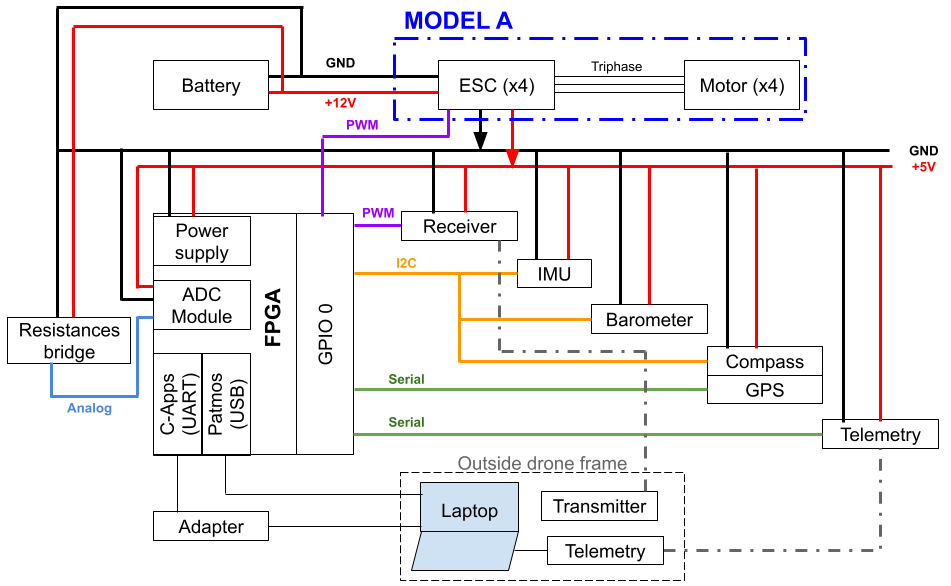
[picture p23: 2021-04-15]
Predict_doc/Figures/hardware/Hardware_diagramA_ADC.png

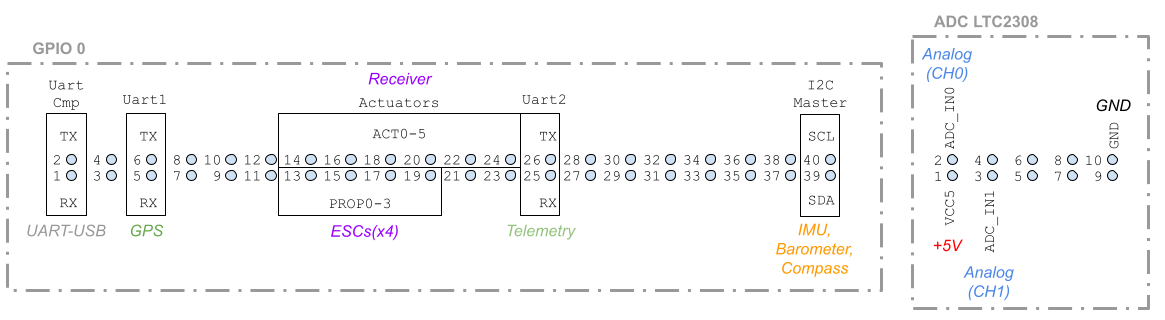
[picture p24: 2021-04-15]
Predict_doc/Figures/hardware/FPGA_pins_ADC.png

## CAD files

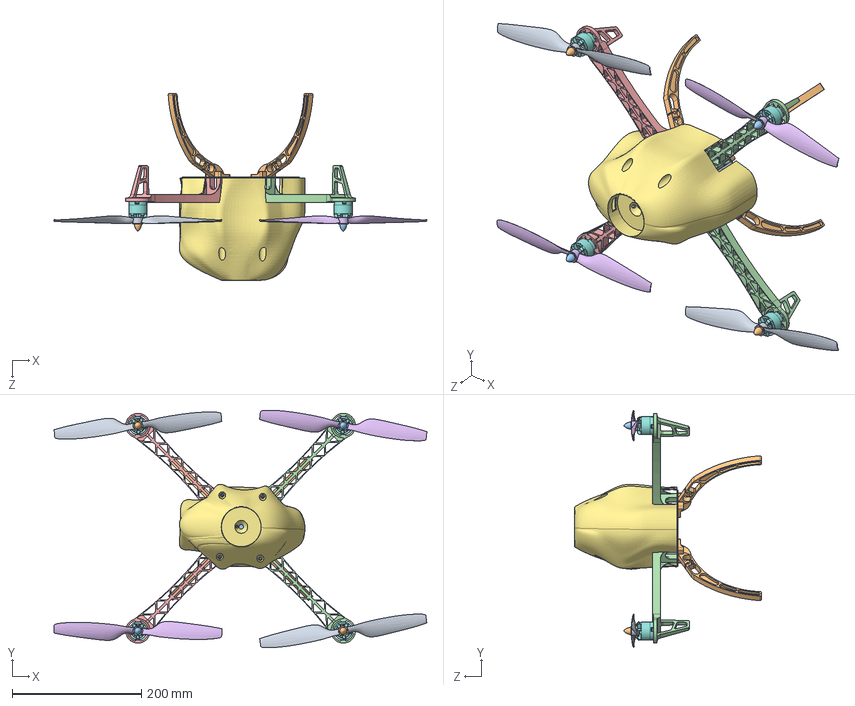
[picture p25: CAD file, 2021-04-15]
hardware_design/CAD_files/frame_complete_modelB.SLDASM
578.1 x 367.9 x 289.5 mm
bottom
leg x 4
top
arm_red x 2
arm_white x 2
propeller x 2
cover
motorB x 4
propeller_mirrorB x 2
motor_topB2 x 2
motor_topB x 2

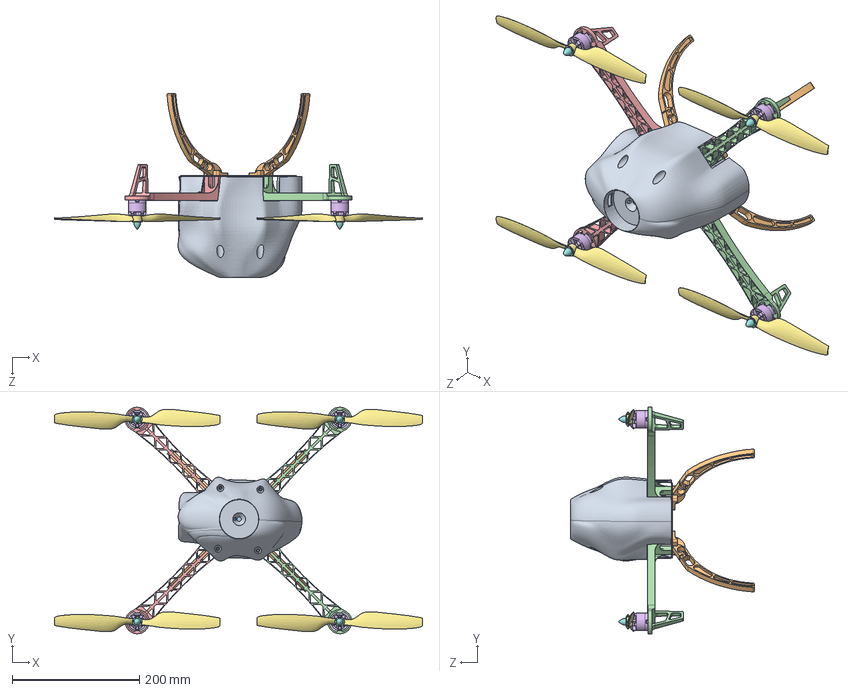
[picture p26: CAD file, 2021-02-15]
hardware_design/CAD_files/frame_assembled.SLDASM
578.2 x 356.2 x 289.5 mm
bottom
leg x 4
top
arm_red x 2
arm_white x 2
motor x 4
propeller x 4
motor_top x 4
cover

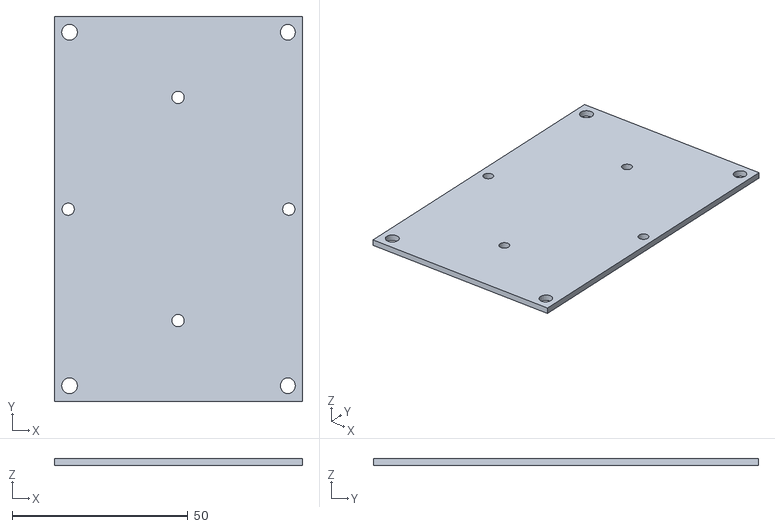
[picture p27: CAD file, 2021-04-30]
hardware_design/3D_printing/FPGA_attachment.stl
70.6 x 109.5 x 2.00

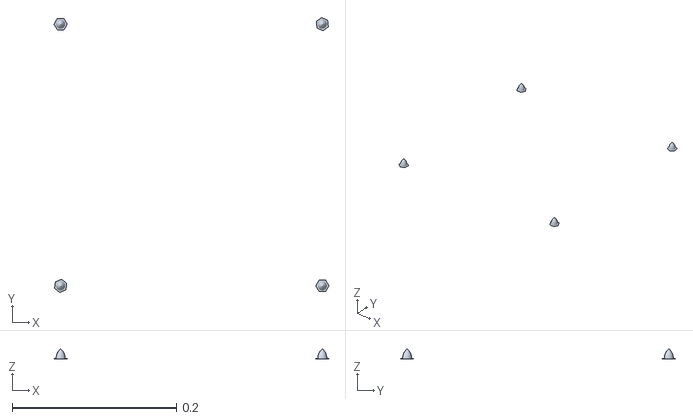
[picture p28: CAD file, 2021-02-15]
hardware_design/urdf_export/frame_complete.SLDASM/meshes/tops.STL
0.334 x 0.334 x 0.0125

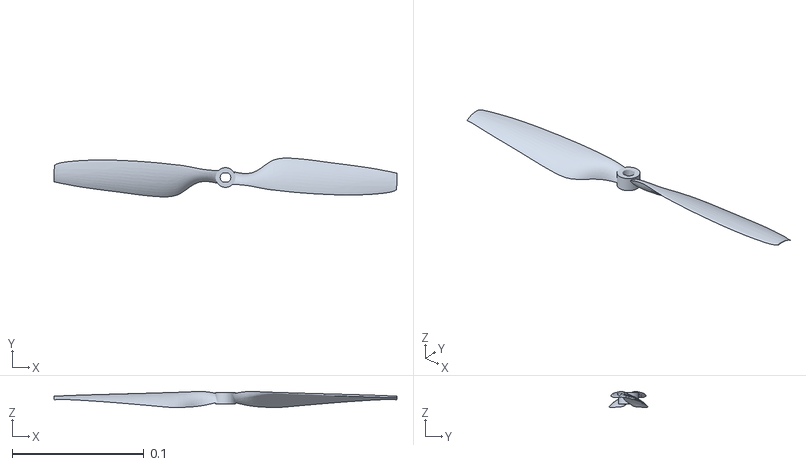
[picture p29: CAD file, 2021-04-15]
hardware_design/urdf_export/frame_complete_modelB.SLDASM/meshes/motor3.STL
0.26 x 0.0294 x 0.0122

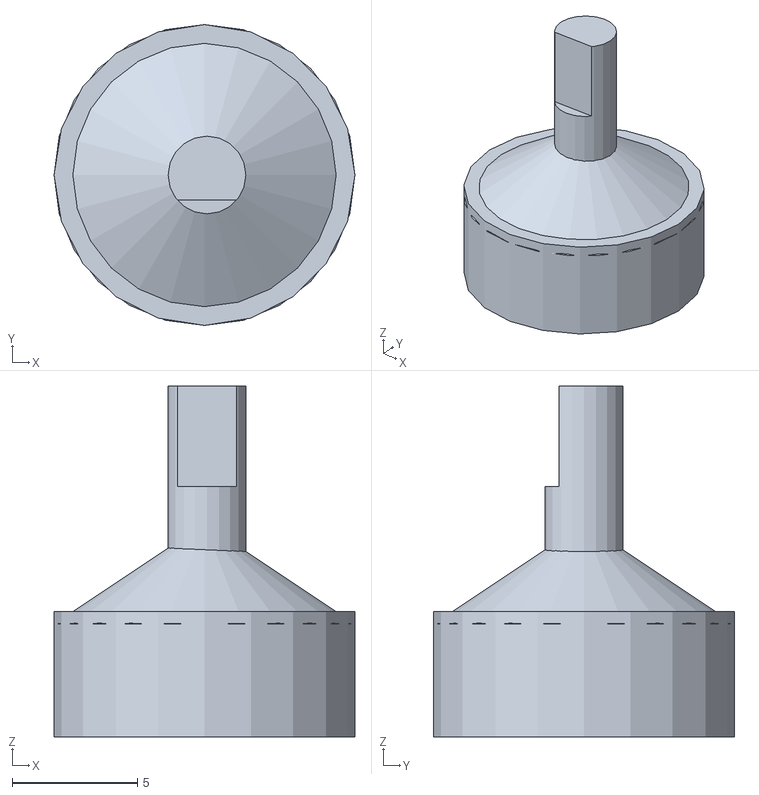
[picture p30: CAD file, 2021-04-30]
hardware_design/3D_printing/GPS_support.stl
12.0 x 12.0 x 14.0

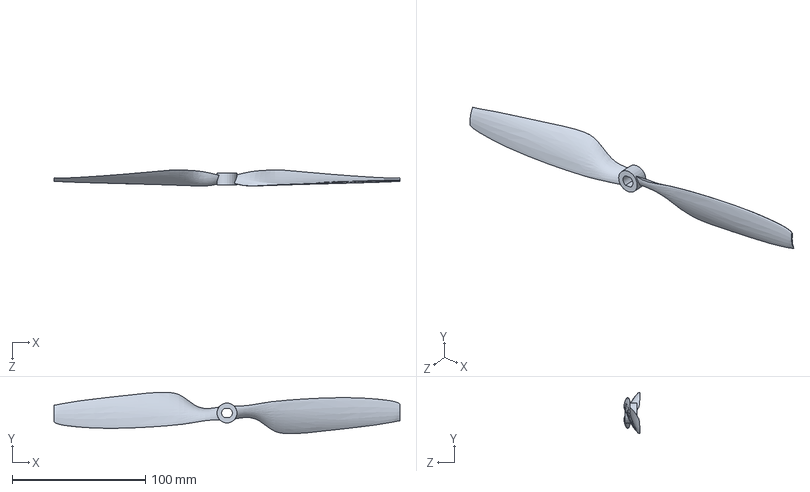
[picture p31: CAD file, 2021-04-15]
hardware_design/CAD_files/propeller_mirrorB.sldprt
260.0 x 31.1 x 12.2 mm

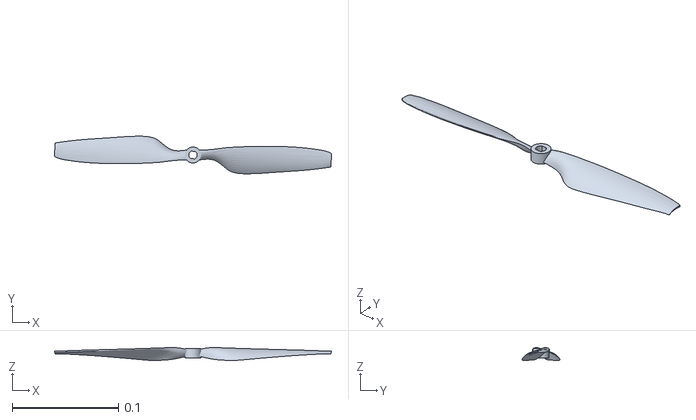
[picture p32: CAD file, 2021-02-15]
hardware_design/urdf_export/frame_complete.SLDASM/meshes/motor2.STL
0.26 x 0.0353 x 0.0122

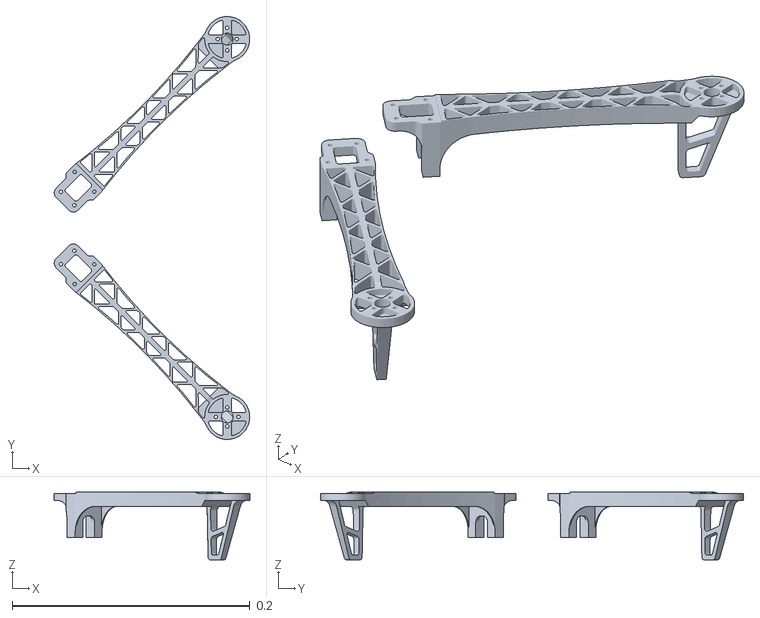
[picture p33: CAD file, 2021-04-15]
hardware_design/urdf_export/frame_complete_modelB.SLDASM/meshes/front.STL
0.165 x 0.356 x 0.057

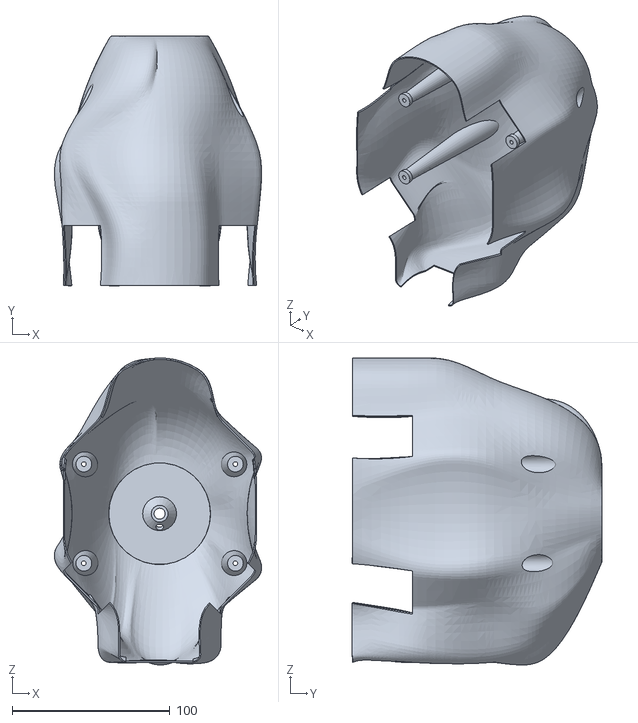
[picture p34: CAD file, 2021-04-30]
hardware_design/3D_printing/Cover_fpga_V13.STL
131.5 x 158.8 x 194.8

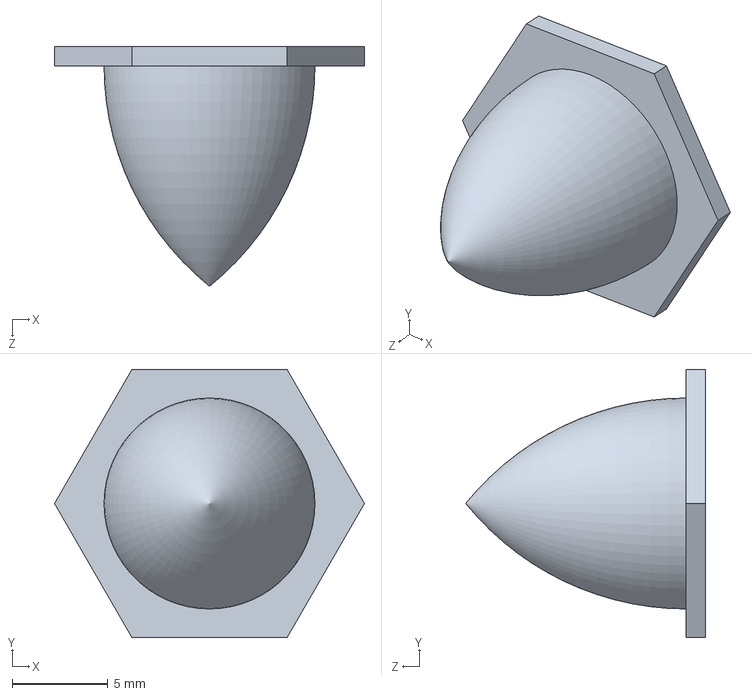
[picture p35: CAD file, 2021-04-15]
hardware_design/CAD_files/motor_topB2.SLDPRT
16.2 x 14.0 x 12.5 mm

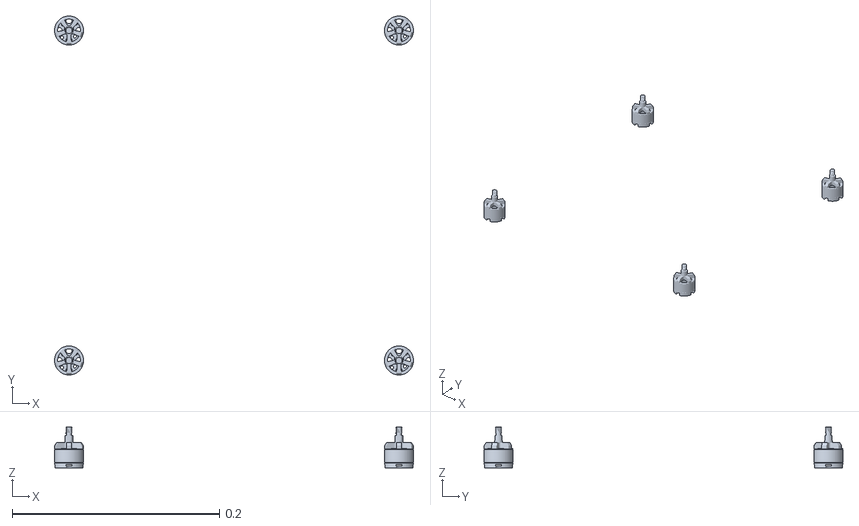
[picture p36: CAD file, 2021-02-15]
hardware_design/urdf_export/frame_complete.SLDASM/meshes/motors.STL
0.346 x 0.346 x 0.0395

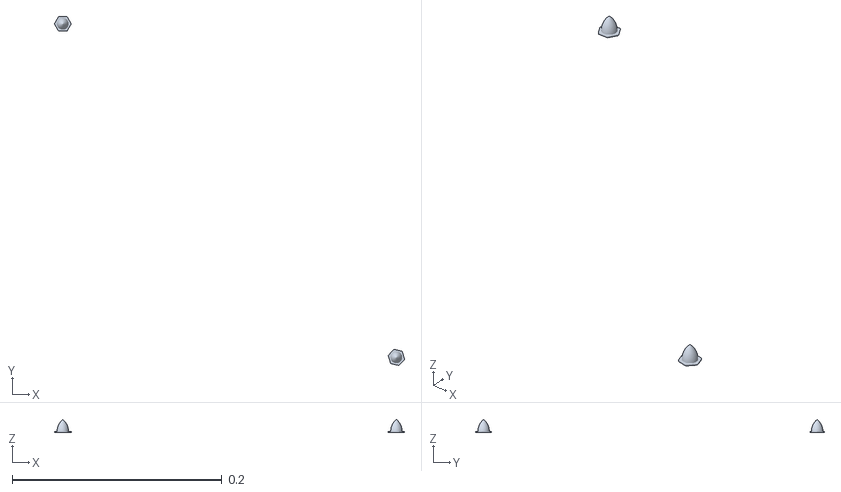
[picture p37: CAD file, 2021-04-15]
hardware_design/urdf_export/frame_complete_modelB.SLDASM/meshes/tops.STL
0.334 x 0.333 x 0.0125

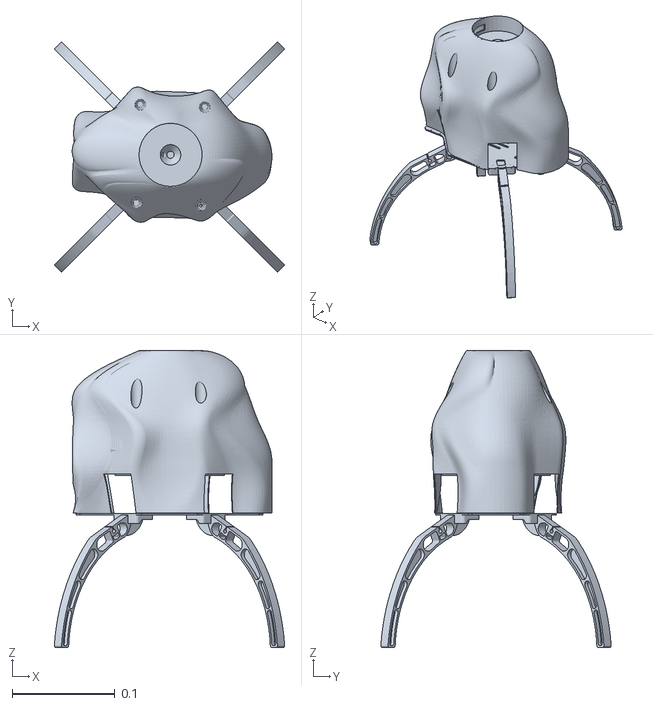
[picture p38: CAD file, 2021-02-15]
hardware_design/urdf_export/frame_complete.SLDASM/meshes/PREDICT.STL
0.225 x 0.225 x 0.289

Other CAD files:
hardware_design/CAD_files/frame_complete.SLDASM
hardware_design/CAD_files/motor_topB.SLDPRT
hardware_design/urdf_export/frame_complete_modelB.SLDASM/meshes/back.STL
hardware_design/CAD_files/motorB.SLDPRT
hardware_design/CAD_files/arm_red.SLDPRT
hardware_design/CAD_files/arm_white.SLDPRT
hardware_design/CAD_files/bottom.SLDPRT
hardware_design/CAD_files/leg.SLDPRT
hardware_design/CAD_files/motor.SLDPRT
hardware_design/CAD_files/motor_top.SLDPRT
hardware_design/CAD_files/propeller.SLDPRT
hardware_design/CAD_files/propeller2.SLDPRT
hardware_design/CAD_files/propeller_mirror.sldprt
hardware_design/CAD_files/propeller_test.sldprt
hardware_design/CAD_files/top.SLDPRT
hardware_design/urdf_export/frame_complete.SLDASM/meshes/back.STL
hardware_design/urdf_export/frame_complete.SLDASM/meshes/front.STL
hardware_design/urdf_export/frame_complete.SLDASM/meshes/motor1.STL
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

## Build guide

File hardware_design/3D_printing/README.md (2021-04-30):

# 3D Printing files #

This folder contains the custom hardware parts in .STL format, which is compatible with most of 3D printers.

### Notes ### 

The FPGA-attachment and GPS-support were done using a [Markerbot Method X](https://store.makerbot.com/method-x)

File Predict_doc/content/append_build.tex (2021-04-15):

\chapter{Appendix: how to assemble the drone}\label{app:build}
This chapter describes how to build and assemble all the components for both drone models presented in Chapter \ref{ch:hw} and it is useful for readers that do not find the present hardware design intuitive or that are not familiar with these DIY projects.

\section*{Board and sensors}

\begin{enumerate}
    \item On the PCB bottom side, soldier sets of female pins for the ADC module and the GPIO0. 
    On the top side, soldier the resistances and sets of male pins for the ESCs, telemetry and GPS-compass; soldier sets of female pins for the receiver, UART-USB adapter, the barometer and IMU.

    For the battery feedback and power supply pins (for the FPGA, and the +5v coming from the power module in Model-B units) the ground pins are male and voltage input are female.
    
\begin{figure} [H]
    \centering
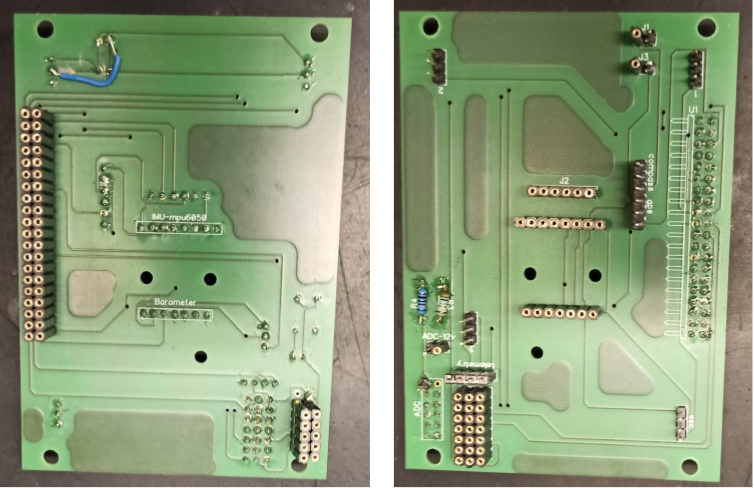
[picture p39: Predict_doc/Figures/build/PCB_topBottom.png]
    
    \caption{Pins soldier to the PCB on the bottom side (left) and top (right).}
    \label{fig:build_pins}
\end{figure}
    
    \item To attach the PCB to the FPGA, it is necessary to make the female pins on the bottom side longer, so add a second round of female pins on top of the soldiered ones. Once the PCB can be placed on top of the FPGA, use screws M3 on the corners to attach it.

    \item Add the IMU, barometer, UART-USB adapter and receiver to the top side of the PCB. Watch out for the height of the sensors.

    \item Attach the steppers to the central holes of the FPGA-Frame attachment. Afterwards, attach the part to the bottom of the FPGA.
    
\end{enumerate}

\begin{figure} [H]
    \centering
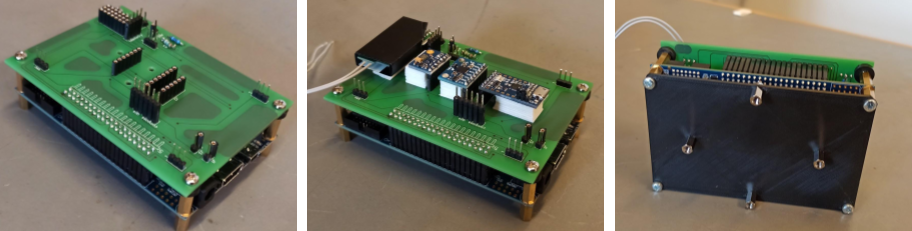
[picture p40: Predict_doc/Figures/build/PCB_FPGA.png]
    
    \caption{Board building steps nr.2 (left), 3 (center) and 4 (right).}
    \label{fig:build_board}
\end{figure}

\section*{Main body assembly}

\begin{enumerate}
    \item Soldier the ESCs power supply and battery X66 connector to the bottom part of the frame.
    
    \item Soldier as well two additional wires for the battery feedback on the top-right ESC. It is not mandatory that the wires are blue, but this color was chosen for this project since it makes it easier to differentiate from the other components.
    
    \item Screw the arms and legs to the bottom part of the frame. Also attach with a zip or tape the ESCs to the arms. As a convenience, the two red arms are meant for the front side and the two white for the back.
    
    \item Turn the body upside down and screw the top part of the frame (except for the screws that are for the cover).
    
\begin{figure} [H]
    \centering
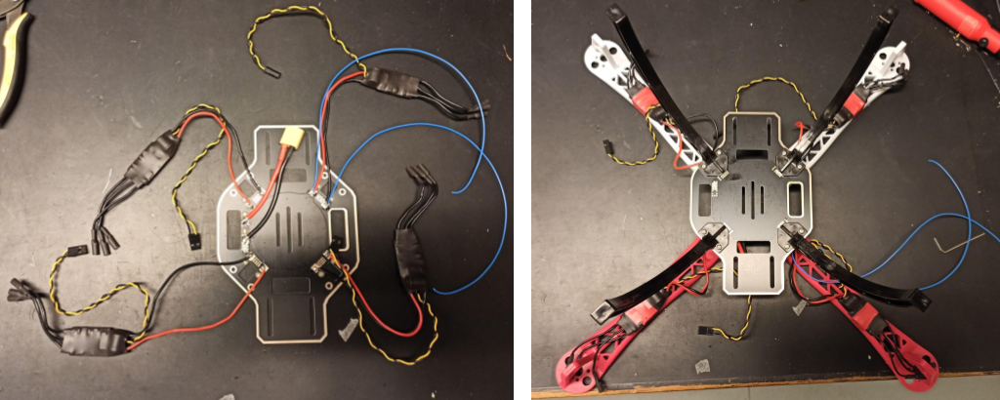
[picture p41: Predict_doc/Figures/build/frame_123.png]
    
    \caption{Frame building steps nr.1 and 2 (left), 3 and 4 (right).}
    \label{fig:build_frame1234}
\end{figure}
    
    \item Screw the motors on the arms and connect them to the ESCs. DO NOT zip/tape these connectors yet.
    
    \item Add a belt for the battery on the bottom. In case of building a Model-B unit, also connect the power module to the battery connector of the bottom.
    
    \item Attach the telemetry module to the top. Watch out for the screws on the top and avoid covering the holes for the FPGA and cover.
    
\begin{figure} [H]
    \centering
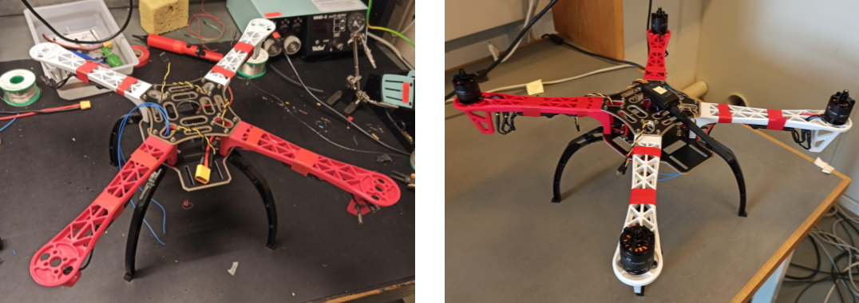
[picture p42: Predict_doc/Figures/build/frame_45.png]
    
    \caption{Frame building steps nr.5 and 6 (left), 7 (right).}
    \label{fig:build_frame567}
\end{figure}

    \item Attach the FPGA+PCB from the previous section with the steppers. Notice that the IMU's X axis must point to the front. For a more visual understanding, the receiver placement must be between the two red arms.
    
    \item Connect the ESCs, telemetry and battery feedback to the board.
    
    \item To download a C-App without removing the cover, add a USB connector (male USB-B mini - female USB) that goes from the UART-USB adapter to the outside of the frame (just down the bottom part, see Figure \ref{fig:hw_space}).
    
    \item Add the drone number to the cover and attach the GPS to its cavity using the CGPS-Cover attachment. It is not mandatory that the drone number is the same as the telemetry pair number, but this makes it easier for working with multiple drones.
    
\begin{figure} [H]
    \centering
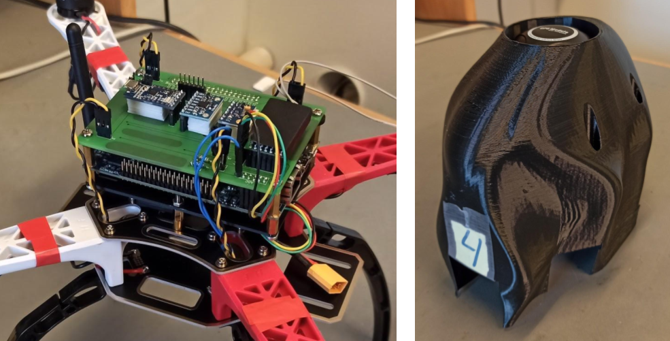
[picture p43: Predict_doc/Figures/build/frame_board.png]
    
    \caption{Frame complete wiring (left) and finished cover (right).}
    \label{fig:build_frameBoard}
\end{figure}
    
    \item Connect the GPS to the PCB and screw the cover to the frame.
    
    \item In case of using a brand new set of motors, run the ESC calibration program to enable the motors and make them work properly.
    
    \item Run the test program for the motors and verify that the four motors spin in the correct direction. In case a motor spins in the wrong direction, switch two of its connections with the ESC.
    
\end{enumerate}

\textbf{\textit{NOTE:}} Before attaching the cover to the frame, check that the devices and the board are functional. Download Patmos and run the test programs for all the devices to verify the components are functional. Check the Appendix \ref{app:setup} to see how to do so.

In case of some devices, it is necessary to modify their settings when they are brand new (or used for the first time) in order to be compatible work with Patmos and the flight controller, see the Section \ref{app:sec_fc}.

% ===================================================================================
% Add this chapter to the table of contents:
%\addcontentsline{toc}{chapter}{Appendix: how to assemble the drone}

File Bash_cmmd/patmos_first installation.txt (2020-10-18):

#Several packages need to be installed. The following apt-get lists the packages that need to be installed on a Ubuntu Linux:

sudo apt install git openjdk-8-jdk gitk cmake make g++ texinfo flex bison \
  subversion libelf-dev graphviz libboost-dev libboost-program-options-dev ruby-full \
  liblpsolve55-dev python zlib1g-dev gtkwave gtkterm scala autoconf libfl2 expect

# Install sbt with:

echo "deb https://dl.bintray.com/sbt/debian /" | sudo tee -a /etc/apt/sources.list.d/sbt.list
sudo apt-key adv --keyserver hkp://keyserver.ubuntu.com:80 \
  --recv 2EE0EA64E40A89B84B2DF73499E82A75642AC823
sudo apt-get update
sudo apt-get install sbt

# We assume that the T-CREST project will live in $HOME/t-crest. Before building the compiler, add the path to the compiler executables into your .bashrc or .profile:

export PATH=$PATH:$HOME/t-crest/local/bin

#install verilator

git clone https://github.com/verilator/verilator
unset VERILATOR_ROOT
cd verilator
git checkout v4.028 #Tested version - newer should be fine
autoconf
./configure
make
sudo make install

# Patmos and the compiler can be checked out from GitHub and are built as follows:

mkdir ~/t-crest
cd ~/t-crest
git clone https://github.com/t-crest/patmos-misc.git misc
./misc/build.sh

###to check if everything is ok
patmos-clang --version

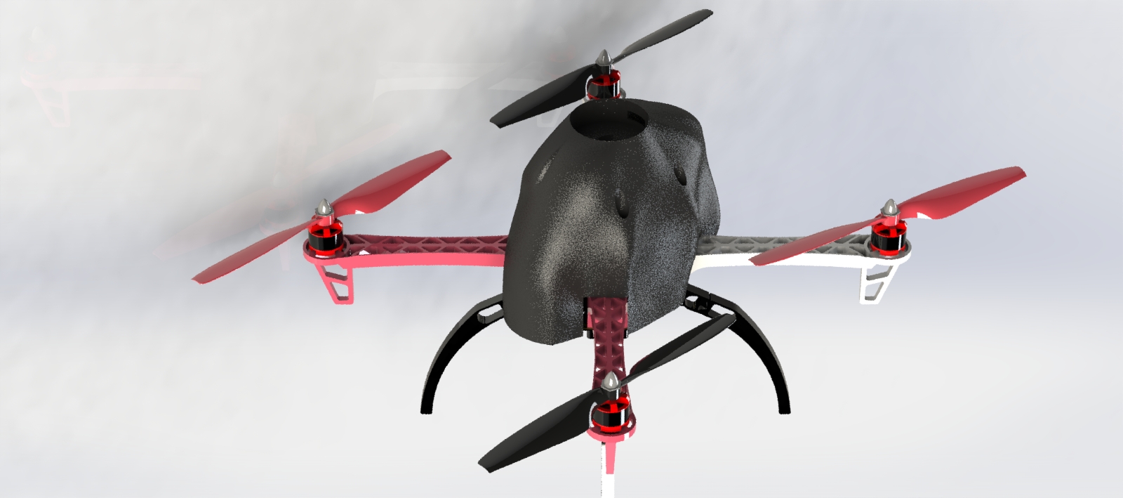
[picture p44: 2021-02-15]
Predict_doc/Figures/hardware/render_assemblyA.JPG

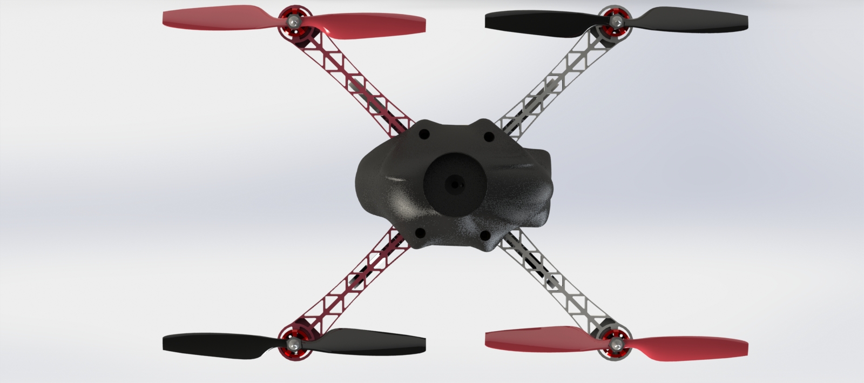
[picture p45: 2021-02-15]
Predict_doc/Figures/hardware/render_assembly_topA.JPG

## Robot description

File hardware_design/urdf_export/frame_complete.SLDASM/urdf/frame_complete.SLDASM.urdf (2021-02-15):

<?xml version="1.0" encoding="utf-8"?>
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
<robot name="frame_complete.SLDASM">
  <link name="PREDICT">
    <inertial>
      <origin xyz="6.5679E-06 0.00020921 -0.047217" rpy="0 0 0" />
      <mass value="0.7905" />
      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
    </inertial>
    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
  </link>
  <link name="motor1">
    <inertial>
      <origin xyz="1.3707E-06 -7.1649E-08 0.029837" rpy="0 0 0" />
      <mass value="0.070504" />
      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
    </inertial>
    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
  </link>
  <joint name="m1" type="continuous">
    <origin xyz="0.15909 0.15911 -0.0015" rpy="0 0 0" />
    <parent link="PREDICT" />
    <child link="motor1" />
    <axis xyz="0 0 -1" />
    <limit lower="-3.1416" upper="3.1416" effort="1000" velocity="1000" />
  </joint>
  <link name="motor2">
    <inertial>
      <origin xyz="2.4517E-08 5.6403E-09 0.029837" rpy="0 0 0" />
      <mass value="0.0090069" />
      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
    </inertial>
    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
  </link>
  <joint name="m2" type="continuous">
    <origin xyz="-0.15911 0.15909 -0.0015" rpy="0 0 0" />
    <parent link="PREDICT" />
    <child link="motor2" />
    <axis xyz="0 0 -1" />
    <limit lower="-3.1416" upper="3.1416" effort="1000" velocity="1000" />
  </joint>
  <link name="motor3">
    <inertial>
      <origin xyz="1.3663E-06 -7.0998E-08 0.029837" rpy="0 0 0" />
      <mass value="0.070504" />
      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
    </inertial>
    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
  </link>
  <joint name="m3" type="continuous">
    <origin xyz="-0.15909 -0.15911 -0.0015" rpy="0 0 0" />
    <parent link="PREDICT" />
    <child link="motor3" />
    <axis xyz="0 0 -1" />
    <limit lower="-3.1416" upper="3.1416" effort="1000" velocity="1000" />
  </joint>
  <link name="motor4">
    <inertial>
      <origin xyz="-7.2389E-08 -3.6433E-09 0.029837" rpy="0 0 0" />
      <mass value="0.009007" />
      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
    </inertial>
    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
  </link>
  <joint name="m4" type="continuous">
    <origin xyz="0.15911 -0.15909 -0.0015" rpy="0 0 0" />
    <parent link="PREDICT" />
    <child link="motor4" />
    <axis xyz="0 0 -1" />
    <limit lower="-3.1416" upper="3.1416" effort="1000" velocity="1000" />
  </joint>
  <link name="front">
    <inertial>
      <origin xyz="0.090922 6.9394E-06 -0.011302" rpy="0 0 0" />
      <mass value="0.58205" />
      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
    </inertial>
    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
  </link>
  <joint name="front_fixed" type="fixed">
    <origin xyz="0 0 0" rpy="0 0 0" />
    <parent link="PREDICT" />
    <child link="front" />
    <axis xyz="0 0 0" />
  </joint>
  <link name="back">
    <inertial>
      <origin xyz="-0.090922 -6.9394E-06 -0.011302" rpy="0 0 0" />
      <mass value="0.58205" />
      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
    </inertial>
    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
  </link>
  <joint name="back_fixed" type="fixed">
    <origin xyz="0 0 0" rpy="0 0 0" />
    <parent link="PREDICT" />
    <child link="back" />
    <axis xyz="0 0 0" />
  </joint>
  <link name="motors">
    <inertial>
      <origin xyz="2.31E-07 -4.4315E-07 0.011837" rpy="0 0 0" />
      <mass value="0.20746" />
      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
    </inertial>
    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
  </link>
  <joint name="m_fixed" type="fixed">
    <origin xyz="0 0 0" rpy="0 0 0" />
    <parent link="PREDICT" />
    <child link="motors" />
    <axis xyz="0 0 0" />
    <limit lower="-3.1416" upper="3.1416" effort="1000" velocity="1000" />
  </joint>
  <link name="tops">
    <inertial>
      <origin xyz="1.3427E-05 2.5905E-06 0.036158" rpy="0 0 0" />
      <mass value="0.016979" />
      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
    </inertial>
    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
  </link>
  <joint name="tops_fixed" type="fixed">
    <origin xyz="0 0 0" rpy="0 0 0" />
    <parent link="PREDICT" />
    <child link="tops" />
    <axis xyz="0 0 0" />
  </joint>
</robot>

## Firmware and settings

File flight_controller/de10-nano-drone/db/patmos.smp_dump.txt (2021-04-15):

State Machine - |patmos_top|Patmos:Patmos_inst_0|SPIMaster:SPIMaster|state
Name state.01 
state.00 0 
state.01 1 

State Machine - |patmos_top|Patmos:Patmos_inst_0|I2CMaster:I2CMaster|busState
Name busState.11 busState.10 busState.01 busState.00 
busState.00 0 0 0 0 
busState.01 0 0 1 1 
busState.10 0 1 0 1 
busState.11 1 0 0 1 

State Machine - |patmos_top|Patmos:Patmos_inst_0|PatmosCore:cores_3|DataCache:dcache|WriteNoBuffer:wc|state
Name state.00 state.10 state.01 
state.00 0 0 0 
state.01 1 0 1 
state.10 1 1 0 

State Machine - |patmos_top|Patmos:Patmos_inst_0|PatmosCore:cores_3|DataCache:dcache|NullCache:bp|stateReg
Name stateReg.00 stateReg.10 stateReg.01 
stateReg.00 0 0 0 
stateReg.01 1 0 1 
stateReg.10 1 1 0 

State Machine - |patmos_top|Patmos:Patmos_inst_0|PatmosCore:cores_3|DataCache:dcache|StackCache:sc|stateReg
Name stateReg.110 stateReg.101 stateReg.100 stateReg.011 stateReg.010 stateReg.001 stateReg.000 
stateReg.000 0 0 0 0 0 0 0 
stateReg.001 0 0 0 0 0 1 1 
stateReg.010 0 0 0 0 1 0 1 
stateReg.011 0 0 0 1 0 0 1 
stateReg.100 0 0 1 0 0 0 1 
stateReg.101 0 1 0 0 0 0 1 
stateReg.110 1 0 0 0 0 0 1 

State Machine - |patmos_top|Patmos:Patmos_inst_0|PatmosCore:cores_3|DataCache:dcache|DirectMappedCache:dm|stateReg
Name stateReg.11 stateReg.10 stateReg.01 stateReg.00 
stateReg.00 0 0 0 0 
stateReg.01 0 0 1 1 
stateReg.10 0 1 0 1 
stateReg.11 1 0 0 1 

State Machine - |patmos_top|Patmos:Patmos_inst_0|PatmosCore:cores_3|MCache:icache|MCacheCtrl:ctrl|stateReg
Name stateReg.110 stateReg.101 stateReg.100 stateReg.011 stateReg.010 stateReg.001 stateReg.000 
stateReg.000 0 0 0 0 0 0 0 
stateReg.001 0 0 0 0 0 1 1 
stateReg.010 0 0 0 0 1 0 1 
stateReg.011 0 0 0 1 0 0 1 
stateReg.100 0 0 1 0 0 0 1 
stateReg.101 0 1 0 0 0 0 1 
stateReg.110 1 0 0 0 0 0 1 

State Machine - |patmos_top|Patmos:Patmos_inst_0|PatmosCore:cores_2|DataCache:dcache|WriteNoBuffer:wc|state
Name state.00 state.10 state.01 
state.00 0 0 0 
state.01 1 0 1 
state.10 1 1 0 

State Machine - |patmos_top|Patmos:Patmos_inst_0|PatmosCore:cores_2|DataCache:dcache|NullCache:bp|stateReg
Name stateReg.00 stateReg.10 stateReg.01 
stateReg.00 0 0 0 
stateReg.01 1 0 1 
stateReg.10 1 1 0 

State Machine - |patmos_top|Patmos:Patmos_inst_0|PatmosCore:cores_2|DataCache:dcache|StackCache:sc|stateReg
Name stateReg.110 stateReg.101 stateReg.100 stateReg.011 stateReg.010 stateReg.001 stateReg.000 
stateReg.000 0 0 0 0 0 0 0 
stateReg.001 0 0 0 0 0 1 1 
stateReg.010 0 0 0 0 1 0 1 
stateReg.011 0 0 0 1 0 0 1 
stateReg.100 0 0 1 0 0 0 1 
stateReg.101 0 1 0 0 0 0 1 
stateReg.110 1 0 0 0 0 0 1 

State Machine - |patmos_top|Patmos:Patmos_inst_0|PatmosCore:cores_2|DataCache:dcache|DirectMappedCache:dm|stateReg
Name stateReg.11 stateReg.10 stateReg.01 stateReg.00 
stateReg.00 0 0 0 0 
stateReg.01 0 0 1 1 
stateReg.10 0 1 0 1 
stateReg.11 1 0 0 1 

State Machine - |patmos_top|Patmos:Patmos_inst_0|PatmosCore:cores_2|MCache:icache|MCacheCtrl:ctrl|stateReg
Name stateReg.110 stateReg.101 stateReg.100 stateReg.011 stateReg.010 stateReg.001 stateReg.000 
stateReg.000 0 0 0 0 0 0 0 
stateReg.001 0 0 0 0 0 1 1 
stateReg.010 0 0 0 0 1 0 1 
stateReg.011 0 0 0 1 0 0 1 
stateReg.100 0 0 1 0 0 0 1 
stateReg.101 0 1 0 0 0 0 1 
stateReg.110 1 0 0 0 0 0 1 

State Machine - |patmos_top|Patmos:Patmos_inst_0|PatmosCore:cores_1|DataCache:dcache|WriteNoBuffer:wc|state
Name state.00 state.10 state.01 
state.00 0 0 0 
state.01 1 0 1 
state.10 1 1 0 

State Machine - |patmos_top|Patmos:Patmos_inst_0|PatmosCore:cores_1|DataCache:dcache|NullCache:bp|stateReg
Name stateReg.00 stateReg.10 stateReg.01 
stateReg.00 0 0 0 
stateReg.01 1 0 1 
stateReg.10 1 1 0 

State Machine - |patmos_top|Patmos:Patmos_inst_0|PatmosCore:cores_1|DataCache:dcache|StackCache:sc|stateReg
Name stateReg.110 stateReg.101 stateReg.100 stateReg.011 stateReg.010 stateReg.001 stateReg.000 
stateReg.000 0 0 0 0 0 0 0 
stateReg.001 0 0 0 0 0 1 1 
stateReg.010 0 0 0 0 1 0 1 
stateReg.011 0 0 0 1 0 0 1 
stateReg.100 0 0 1 0 0 0 1 
stateReg.101 0 1 0 0 0 0 1 
stateReg.110 1 0 0 0 0 0 1 

State Machine - |patmos_top|Patmos:Patmos_inst_0|PatmosCore:cores_1|DataCache:dcache|DirectMappedCache:dm|stateReg
Name stateReg.11 stateReg.10 stateReg.01 stateReg.00 
stateReg.00 0 0 0 0 
stateReg.01 0 0 1 1 
stateReg.10 0 1 0 1 
stateReg.11 1 0 0 1 

State Machine - |patmos_top|Patmos:Patmos_inst_0|PatmosCore:cores_1|MCache:icache|MCacheCtrl:ctrl|stateReg
Name stateReg.110 stateReg.101 stateReg.100 stateReg.011 stateReg.010 stateReg.001 stateReg.000 
stateReg.000 0 0 0 0 0 0 0 
stateReg.001 0 0 0 0 0 1 1 
stateReg.010 0 0 0 0 1 0 1 
stateReg.011 0 0 0 1 0 0 1 
stateReg.100 0 0 1 0 0 0 1 
stateReg.101 0 1 0 0 0 0 1 
stateReg.110 1 0 0 0 0 0 1 

State Machine - |patmos_top|Patmos:Patmos_inst_0|PatmosCore:cores_0|DataCache:dcache|WriteNoBuffer:wc|state
Name state.00 state.10 state.01 
state.00 0 0 0 
state.01 1 0 1 
state.10 1 1 0
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

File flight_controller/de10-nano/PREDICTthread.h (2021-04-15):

#ifndef PREDICT_Thread_H
#define PREDICT_Thread_H

// **************************
/////   I2C THREAD   /////
// ***********************
// i2c thread core 1
void i2c_thread()
{
    ////////////////////////////
    /////   SETUP PHASE   /////
    //////////////////////////
    gyro_setup();
    // setup_compass();
    // read_compass();                                               //Read and calculate the compass data.
    // pthread_mutex_lock(&mutex);
    // angle_yaw = actual_compass_heading;                           //Set the initial compass heading.
    // pthread_mutex_unlock(&mutex);
    // barometer_setup();
    if(GYRO_CALLIB)callibrate_gyro();
    if(COMP_CALLIB)callibrate_compass();
    if(LEVEL_CALLIB)callibrate_level();
            //Read the MPU-6050
    __uint32_t timer = get_cpu_usecs();

    ///////////////////////////
    /////   MAIN PHASE   /////
    /////////////////////////
    while(!program_off){
        // Update the variables
        pthread_mutex_lock(&mutex);
        pthread_mutex_unlock(&mutex);
        //Read the MPU-6050, barmeter and compass
        // read_compass();
        gyro_signalen();
        // barometer_pressure();
        while (get_cpu_usecs() - timer < dt*1000000); 
        // if(PRINT_COMMANDS)
        // {
        //     pthread_mutex_lock(&printmutex);
        //     printf("\t\t\ti2c: %llu\n",get_cpu_usecs() - timer );
        //     pthread_mutex_unlock(&printmutex);
        // }

        timer = get_cpu_usecs();
    }

}

//receiver thread core 2
void receiver_thread()
{
    while(!program_off)
    {
        pthread_mutex_lock(&mutex);
        pthread_mutex_unlock(&mutex);
        transmitter_read();
    }
}

//gps and telemetry thread core 3 (not used fue to technical difficulties)
void gps_telemetry_thread()
{
    __int32_t lat_gps_previous, lon_gps_previous;
    __int32_t lat_gps_actual, lon_gps_actual;
    float gps_pitch_adjust_north, gps_roll_adjust_north;
    __uint8_t new_line_found, new_gps_data_available;
    __uint8_t gps_rotating_mem_location;
    __int32_t gps_lat_total_avarage, gps_lon_total_avarage;
    __int32_t gps_lat_rotating_mem[40], gps_lon_rotating_mem[40];
    __int32_t gps_lat_error, gps_lon_error;
    __int32_t gps_lat_error_previous, gps_lon_error_previous;
    __uint8_t latitude_north, longiude_east ;
    struct gps_tpv GPS;

    if(PRINT_COMMANDS)printf("gps setup\n");
    gps_init_tpv(&GPS);

    while(!program_off){
        read_gps(&GPS);
        lat_gps_actual = abs((double)GPS.latitude/GPS_LAT_LON_FACTOR);
        lon_gps_actual = abs((double)GPS.longitude/GPS_LAT_LON_FACTOR);

        if(PRINT_COMMANDS)printf("GPS = %d, %d, mode = %d\n", lat_gps_actual, lon_gps_actual, GPS.mode);
        //pthread_mutex_unlock(&mutex);
        
        double alt =  (double)GPS.altitude/GPS_VALUE_FACTOR;

        if (GPS.latitude >0)latitude_north = 1;                                               //When flying north of the equator the latitude_north variable will be set to 1.
        else latitude_north = 0;                                                                           //When flying south of the equator the latitude_north variable will be set to 0.

        if (GPS.longitude >0)longiude_east = 1;                                                //When flying east of the prime meridian the longiude_east variable will be set to 1.
        else longiude_east = 0;

        if(GPS.mode == 3)
        {
            pthread_mutex_lock(&mutex);
            number_used_sats =8;                                             //Filter the number of satillites from the GGA line.
            pthread_mutex_unlock(&mutex);
        }
        else
        {
            pthread_mutex_lock(&mutex);
            number_used_sats =3;
            pthread_mutex_unlock(&mutex);
        }



        if (lat_gps_previous == 0 && lon_gps_previous == 0) {                                              //If this is the first time the GPS code is used.
            lat_gps_previous = lat_gps_actual;                                                               //Set the lat_gps_previous variable to the lat_gps_actual variable.
            lon_gps_previous = lon_gps_actual;                                                               //Set the lon_gps_previous variable to the lon_gps_actual variable.
        }
        l_lat_gps = lat_gps_previous;                                                                      //Set the l_lat_gps variable to the previous latitude value.
        l_lon_gps = lon_gps_previous;                                                                      //Set the l_lon_gps variable to the previous longitude value.

        lat_gps_previous = lat_gps_actual;                                                                 //Remember the new latitude value in the lat_gps_previous variable for the next loop.
        lon_gps_previous = lon_gps_actual;                                                                 //Remember the new longitude value in the lat_gps_previous variable for the next loop.

        // printf("lat_gps_actual: %f  lon_gps_actual: %f\n",(double)GPS.latitude,(double)GPS.longitude );
        if (number_used_sats < 8){if(PRINT_COMMANDS && error_print)printf("not enough satellite to lock on");}                                                              //Turn the LED on the STM solid on (LED function is inverted). Check the STM32 schematic.

        if (flight_mode >= 3 && waypoint_set == 0) {                                                          //If the flight mode is 3 (GPS hold) and no waypoints are set.
            pthread_mutex_lock(&mutex);
            waypoint_set = 1;                                                                                   //Indicate that the waypoints are set.
            l_lat_waypoint = l_lat_gps;                                                                         //Remember the current latitude as GPS hold waypoint.
            l_lon_waypoint = l_lon_gps;                                                                         //Remember the current longitude as GPS hold waypoint.
            pthread_mutex_unlock(&mutex);
        }

        if (flight_mode >= 3 && waypoint_set == 1) {                                                          //If the GPS hold mode and the waypoints are stored.
            //GPS stick move adjustments
            if (flight_mode == 3 && takeoff_detected == 1) {
                if (!latitude_north) {
                    l_lat_gps_float_adjust += 0.0015 * (((channel_2 - 1500) * cos(gps_man_adjust_heading * 0.017453)) + ((channel_1 - 1500) * cos((gps_man_adjust_heading - 90) * 0.017453))); //South correction
                }
                else {
                    l_lat_gps_float_adjust -= 0.0015 * (((channel_2 - 1500) * cos(gps_man_adjust_heading * 0.017453)) + ((channel_1 - 1500) * cos((gps_man_adjust_heading - 90) * 0.017453))); //North correction
                }
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

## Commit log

2020-07-06 Add files via upload
    ADD: flight controller for arduino
2020-07-07 Add files via upload
    Wire Library files
2020-07-08 Added scripts
    Avaliable scripts to run on the terminal for updating, building and downloading patmos on the boards
2020-07-10 Add files via upload
    ADD:IMU code with RPY--to be tested
2020-07-13 UPDATE: working IMU rpy values
2020-07-14 Added drone-motor app
    Still in progress
2020-07-15 Modified drone-motor app
    The motors are working on the PROP pins. An example script has also been added.
2020-07-27 ADD; working IMU code
2020-07-30 ADD: Arduino fc , gps and compass codes
2020-07-31 GPS Neo6M working on Arduino
2020-09-27 NEW: Added barometer file, needs to fix I2C so we can read more than 1 byte of data
2020-11-08 EDIT: Modified the Barometer test file, I2C still doens't work
2021-01-25 ADD: arduino test code for gps
2021-02-15 Added drone frame in CAD and URDF
    [PREDICT.STL, arm_red.SLDPRT, arm_white.SLDPRT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]
2021-04-15 Added hardware design and documentation files
    [PREDICT.STL, arm_red.SLDPRT, arm_white.SLDPRT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]
2021-04-30 Created folder for 3D print
